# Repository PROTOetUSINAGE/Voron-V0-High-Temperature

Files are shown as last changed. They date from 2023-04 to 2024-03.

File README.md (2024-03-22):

# Voron_V0_High_Temperature

The idea  was to make a Voron V0 with the capability of printing high temperature materials like PEI, PEEK ...

A lot of rework was made to be able to fit everything.

I don't even know if we can still call it a Voron V0.

By accident, I maybe design the Smallest High Temp 3D Printer.

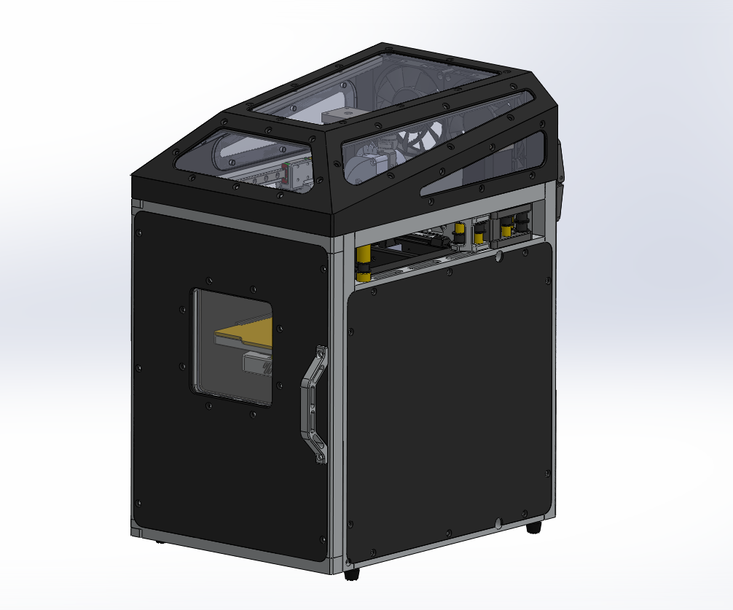
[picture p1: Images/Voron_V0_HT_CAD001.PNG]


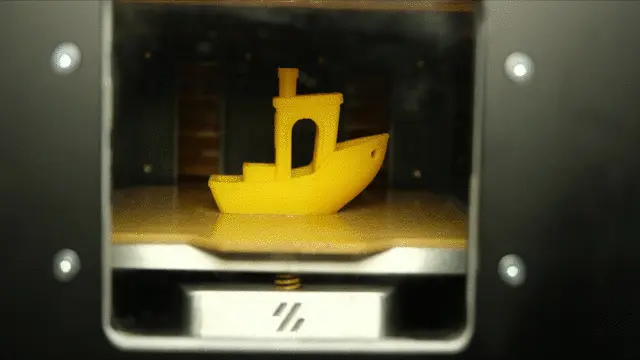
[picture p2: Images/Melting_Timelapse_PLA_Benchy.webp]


## Caracteristics :

- Print volume : 115x115x115mm( a little bits smaller than a V0 )
- Max speed : 500mm/s at 20000mm/s² acceleration
- Max printing speed : around 250mm/s
- Duet3D mini 5+ control board
- Bondtech Mini LGX extruder
- 24V PSU
- Watercooled Hotend Dragon Highflow up to 450°C
- 60W cartridge Heater for the hotend
- Compatible with V6 nozzle ( so I can use brass, copper, steel, ... nozzle )
- Force convection heated chamber up to 230°C 
- 400W 230V cartridge heater with fins for the chamber
- Ø100mm aluminium blower power by a bldc motor 
- Glass fiber reinforce PEI bed
- 100W 230V Silicone heater pad for the bed
- 250°C thermal fuse to protect my house from fire
- Tig welded steel chamber 1mm thick sheet
- CNC milled frame and gantry
- Tig welded aluminium hood with polycarbonate windows and leds
- Custom clamp mechanism for the bed 
- Custom bellow made from PI ( Kapton and PTFE tape)
- Door with borosilicate double glazing 
- Milled Dibond panel
- 7 fans if you count the blower
- The few parts who are 3d printed are made of PEKK-CF
- The printer weighs 10kg ( which is a lot for it size )
- Almost same fooprint as the V0 230x300mm

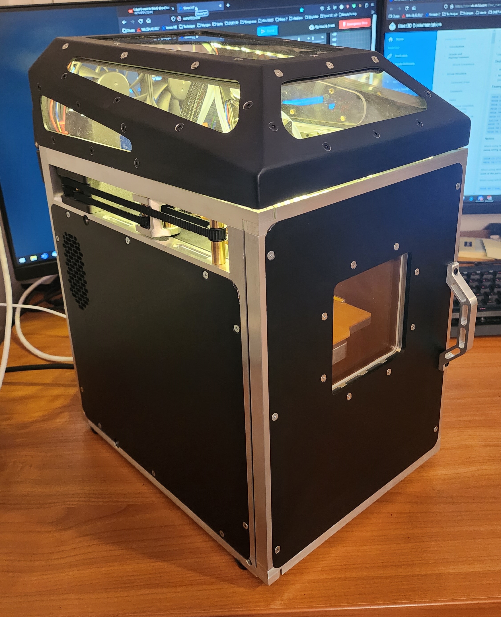
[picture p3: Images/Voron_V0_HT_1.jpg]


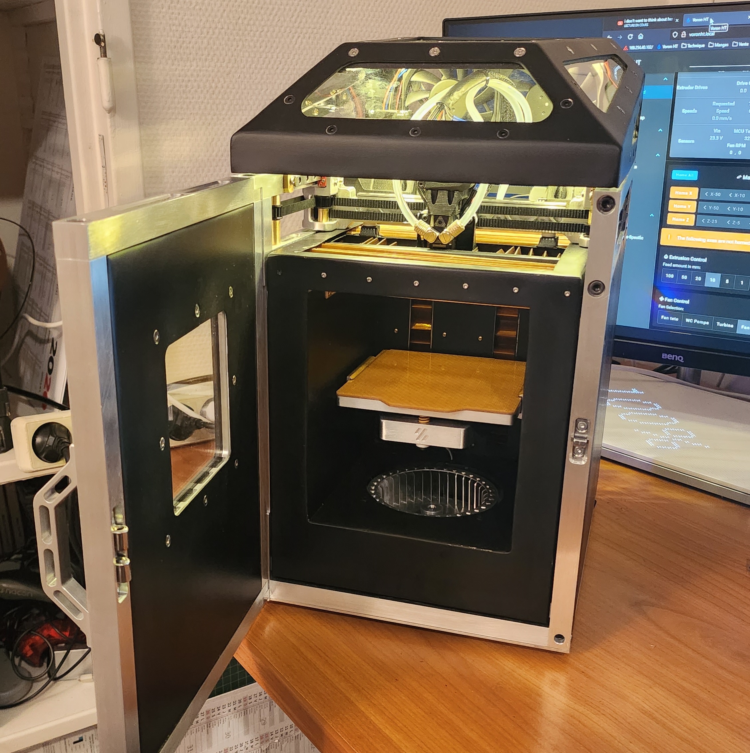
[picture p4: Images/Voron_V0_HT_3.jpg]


Around 800hr was needed to make the first example.

If you want to discuss of the build : [Discord](https://discord.com/channels/840596987522056232/1103065458917261322)

Disclaimer : This build is not supported by Voron Design

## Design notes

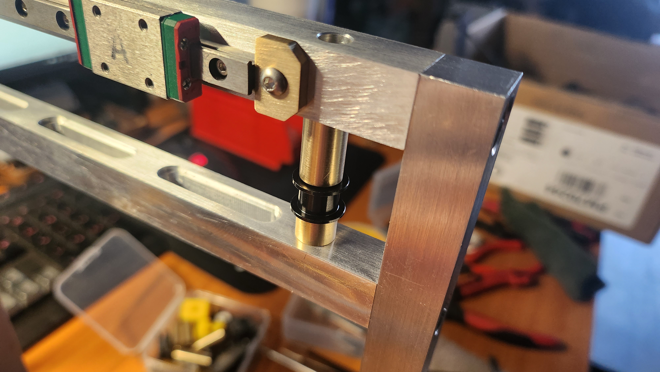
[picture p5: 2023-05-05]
Images/Voron_V0_HT (88).jpg

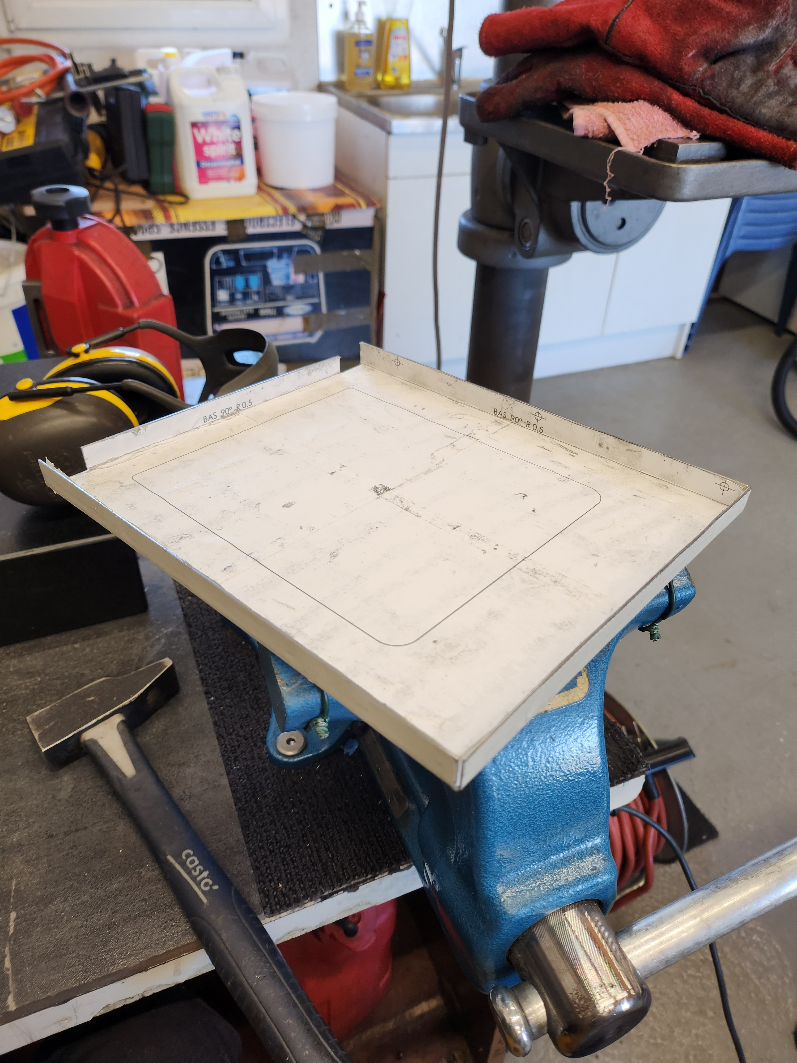
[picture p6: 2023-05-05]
Images/Voron_V0_HT (17).jpg

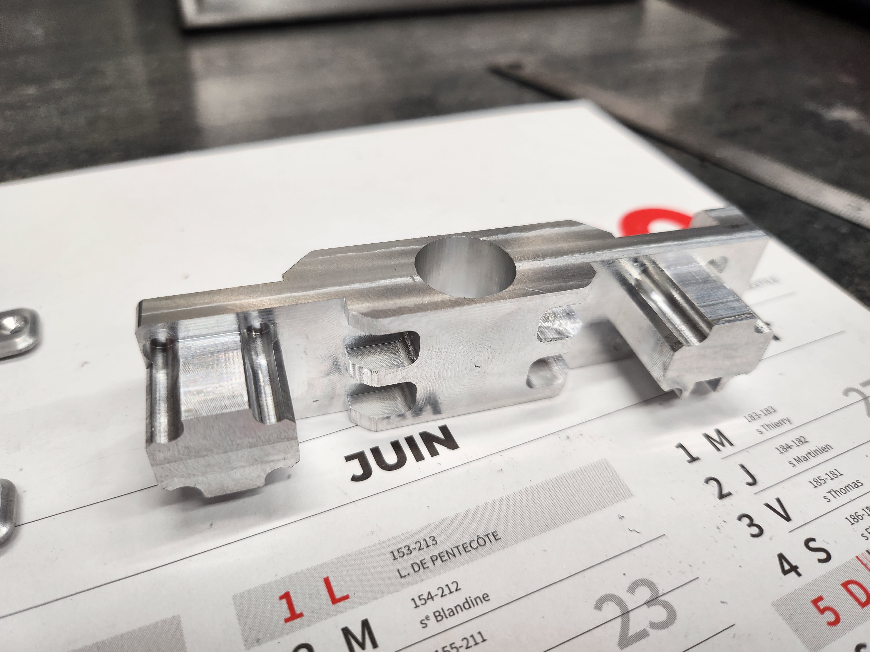
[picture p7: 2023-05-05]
Images/Voron_V0_HT (58).jpg

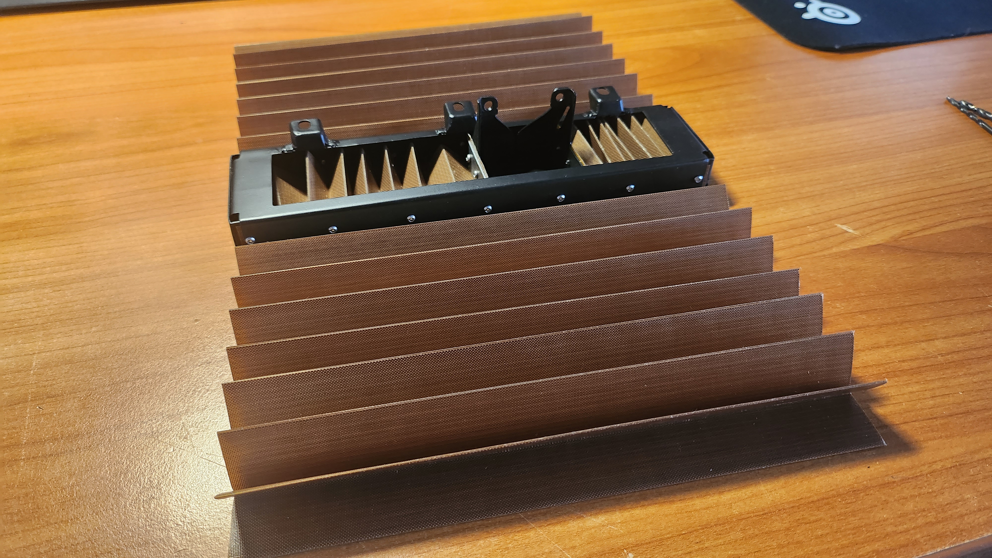
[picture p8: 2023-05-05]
Images/Voron_V0_HT (102).jpg

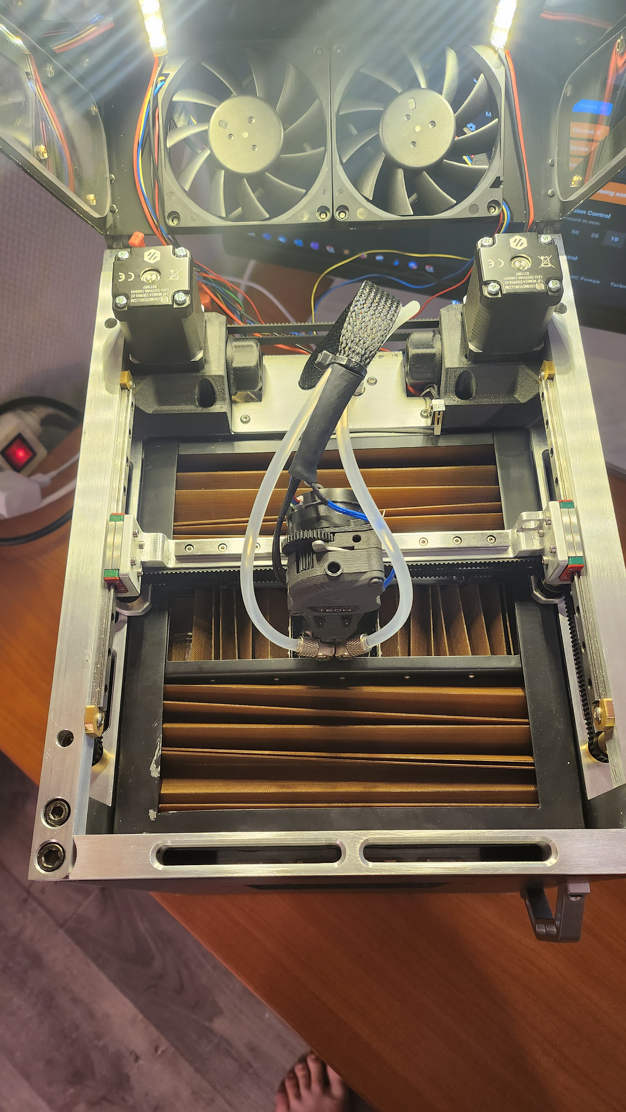
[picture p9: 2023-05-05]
Images/Voron_V0_HT (114).jpg

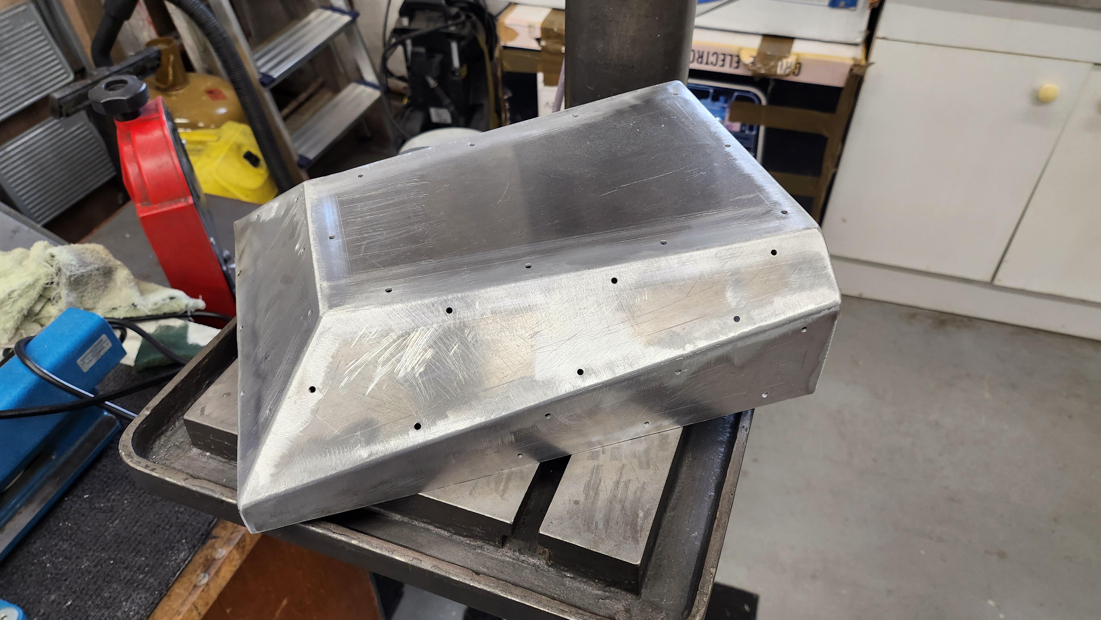
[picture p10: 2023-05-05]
Images/Voron_V0_HT (66).jpg

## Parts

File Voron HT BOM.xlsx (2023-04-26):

Components |  | QTY | Link | Price | Comment
 |  |  | Total = | 1338.70 €
Hardware | M3 Rivnut
 | M3 Brass Insert
 | M3 ceramic washer
 | M5
 | M3
 | M2
Printed parts | Spool_Holder | 1
 | Hood_Hinge_Male | 2
 | Hood_Hinge_Female | 2
 | Hood_LED_Support | 1
 | DC-DC_Converter_Support | 1
 | Cover_230V | 1
 | PSU_Support | 1
 | X_Carriage | 1
 | Cable_Chain_Support | 1
 | Tensioner_Knob | 2
 | BLDC_Support | 1
 | Drive_Tensioner | 2
 | Drive_Frame | 1
 | Drive_Frame_Symmetry | 1
 | Stress_Relief_Bracket | 1
 | Railstop | 8
Machined parts | Window_Support | 1
 | Door_Handle | 1
 | Door_Pivot | 2
 | Front_Cover | 1
 | Hot_Air_Exit | 2
 | Door_Frame | 1
 | Chamber_Fan_Shaft | 1
 | Chamber_Fan_Bearing_Housing | 1
 | Impeller_Cover | 1
 | Bed_Support | 1
 | Z_Support | 1
 | Bed_Clamp | 2
 | Bed | 1
 | Spacer_M3_Ø8 | 6
 | Gantry | 1
 | Spacer_M3_Ø12_Short | 2
 | Spacer_M3_Ø12_Long | 2
 | Side_Cover_Ventilated | 1
 | Side_Cover | 1
 | Frame | 1
Sheet metal parts | Front_Door | 1
 | Radiator_Support | 1
 | Bellow_Clamp_Z | 4
 | Bellow_Clamp_Z_2 | 4
 | Bellow_Clamp_X | 2
 | Bellow_Clamp_Z | 2
 | Fixing_Lug | 3
 | Bottom_Heated_Chamber | 1
 | Inside_Wall | 2
 | L_Heated_Chamber | 2
 | Bellow_Frame | 2
 | Rear_Chamber | 1
 | Middle_Airflow_Path | 1
 | Back_Airflow | 1
 | Front_Airflow | 1
 | Back_Chamber | 1
 | Gantry_Frame_Clamp | 1
 | Heater_Block_Frame | 1
 | Heater_Block_Plate | 1
 | Gantry_Frame | 1
 | Front_Chamber | 1
 | Endstop_Finger | 1
 | Bed_Spring_Clamp | 1
 | Electronic_Access_Plate | 1 |  | 10.00 €
 | Bottom_Plate | 1 |  | 10.00 €
 | Electronic_Plate | 1 |  | 10.00 €
Metal | 15x15X500mm 2017A | 15 |  | 126.00 €
 | 15x162x162 2017A | 1 |  | 29.89 €
 | 50x50x500mm 2017A | 1 |  | 60.30 €
 | 5x120x248mm 2017A | 1 |  | 10.89 €
 | 20x20X500mm 2017A | 1 |  | 11.13 €
 | Ø10x500mm laiton | 1 |  | 6.20 €
 | 3x20x500mm laiton | 1 |  | 5.54 €
 | 1mm Steel Sheet Carbon Steel | 1 |  | 20.00 €
Chamber | 230V Heater Cartridge with fins 200w 80mm | 2 | Aliexpress (https://fr.aliexpress.com/item/1005003240961756.html) | 43.80 €
 | Ø100mm Blower | 1 | Aliexpress (https://fr.aliexpress.com/item/2003966058.html) | 15.45 €
 | Bldc motor 4260 | 1 | Aliexpress (https://fr.aliexpress.com/item/1005003795771959.html) | 24.99 €
 | 60th Pulley GT2 Ø6 | 1 | Aliexpress (https://fr.aliexpress.com/item/1005003339656144.html) | 3.71 €
 | Circlips Ø22mm
 | Bearing 608 2ZZ
 | Silicone grease
 | Courroie gt2 6mm 400lg | 1 | 123courroie (https://www.123courroies.com/courroie-dentee-2mgt-pas-2mm-renforcee/300696-courroie-dentee-400-2mgt6-gates-5414465285899.html) | 8.48 €
Electronics | PSU 150W 24V DC | 1 | Amazon (https://www.amazon.fr/NUOVA-GERMANY-Alimentation-Professionnelle-Transformateur/dp/B09MJHLBQ7) | 17.90 €
 | Raspberry Pi | 1 | Kubii (https://www.kubii.com/fr/cartes-raspberry-pi/2119-raspberry-pi-3-modele-b-1-gb-kubii-652508442174.html) | 52.80 €
 | Duet3 mini 5+ Wifi | 1 | Caribou (https://caribou3d.com/en/electronic-boards-displays/854-duet3-mini5-wifi.html) | 145.00 €
 | NEMA14 Stepper Motor 40Ncm | 2 | Aliexpress (https://fr.aliexpress.com/item/1005002583135981.html) | 86.39 €
 | NEMA17 Stepper Motor (34mm max) with integrated lead screw 200mm T8x8 | 1
 | NEMA14 36mm round pancake Stepper Motor with 10 tooth spur gear (LDO 36STH20-1004AHG) | 1
 | Omron Mouse Button - Micro Switch | 3 | Amazon (https://www.amazon.fr/gp/product/B081TXMD4K/ref=ppx_yo_dt_b_asin_title_o04_s00?ie=UTF8&th=1) | 8.00 €
 | AC Inlet | 1 | Amazon (https://www.amazon.fr/Willwin-IEC320-C14-Inlet-connecteur-Interrupteur-Commutateur/dp/B078PFFL46) | 1.71 €
 | C13 Power Cord | 1
 | Thermal fuse ceramic 230°C 230V 10A | 1 | Aliexpress (https://fr.aliexpress.com/item/32885492280.html) | 0.73 €
 | Fan Noctua NF-A4x20 FLX 12v | 2 | Amazon (https://www.amazon.fr/gp/product/B071J8CZP9/ref=ppx_yo_dt_b_asin_title_o01_s01?ie=UTF8&psc=1) | 29.80 €
 | Stepdown converter DC-DC 5A 5-32V | 2 | Amazon (https://www.amazon.fr/gp/product/B07VQ89RZG/ref=ppx_yo_dt_b_asin_title_o00_s00?ie=UTF8&psc=1) | 8.99 €
 | PT1000 | 3 | Aliexpress (https://fr.aliexpress.com/item/1005003923279506.html) | 54.12 €
 | Hood fan Delta EFC0812DB | 2 | Mouser (https://www.mouser.fr/ProductDetail/Delta-Electronics/EFC0812DB-F00?qs=%2FW4LtXOBxKstDt5MAdb1kQ%3D%3D) | 27.06 €
 | Fan _70mm | 2 | Amazon (https://www.amazon.com/Gelid-Solutions-Silent-40mm-FN-SX04-42/dp/B00BF3UJKC?ref_=ast_sto_dp&th=1) | 16.00 €
 | SSR_10A_240VAC-32DC | 2 | Mouser (https://www.mouser.fr/ProductDetail/Omron-Automation-and-Safety/G3NA-220B-UTU-DC5-24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) | 76.00 €
 | 24V Heater Cartridge 60w | 1 | Aliexpress (https://fr.aliexpress.com/item/4000974620358.html) | 13.52 €
Extruder Hardware | Watercooled Dragon Hotend | 1 | Aliexpress (https://fr.aliexpress.com/item/1005003231830302.html) | 86.86 €
 | Bondtech lgx lite | 1 | 3Djake (https://www.3djake.fr/bondtech/extrudeuse-lgx-lite-sans-moteur-pas-a-pas) | 69.98 €
 | V6 nozzle 0,4mm | 1 |  |  | 1 nickel plated brass nozzle with dragon hotend
Buildplate | Silicone AC 230V Heater 100x100mm 100W | 1 | Aliexpress (https://fr.aliexpress.com/item/1005002731504740.html) | 28.27 €
 | Aluminum Build Plate 120x120mm 8mm Thickness | 1 |  | 10.00 €
 | Yellow die springs 8x4x20mm | 3 | Aliexpress (https://fr.aliexpress.com/item/32977566403.html) | 5.33 €
Motion | MGN7H Linear Rail 150mm | 5 | Aliexpress (https://fr.aliexpress.com/item/1005001843434827.html) | 55.70 €
 | T8 flange Nut 8mm Lead | 1 | Aliexpress (https://fr.aliexpress.com/item/1005002583135981.html) |  | With kit motor
 | GT2 Open Belt 6mm (3 meters) | 1 | Aliexpress (https://fr.aliexpress.com/item/32987817703.html) | 22.35 €
 | GT2 20T (6mm wide) (5mm bore) | 3 | Aliexpress (https://fr.aliexpress.com/item/32995102911.html) | 9.73 €
 | GT2 idler with teeth | 2 | Aliexpress (https://fr.aliexpress.com/item/1005002998469233.html) | 2.18 €
 | GT2 idler without teeth | 10 | Aliexpress | 10.90 €
Watercooling | Radiator 40mmx2 Alphacool | 1 | Aquatuning (https://www.aquatuning.fr/refroidissement-par-eau/radiateurs/radiateurs-aktiv/40mm/15906/alphacool-nexxxos-xt45-plein-de-cuivre-40mm-dual-radiateur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) | 38.79 €
 | Pump G1/4 | 1 | Aliexpress (https://fr.aliexpress.com/item/1005003646698710.html?scm_id=1007.40050.281175.0&scm-url=1007.40050.281175.0) | 21.16 €
Misc. | 7mm x 7mm cable chain | 1 | Aliexpress (https://www.aliexpress.com/p/order/detail.html?orderId=3016825993495175) | 3.20 €
 | Rubber Feet (14x11x9mm) | 4 | Aliexpress (https://fr.aliexpress.com/item/33014925172.html) | 0.28 €
 | Bowden Tubing 4mmOD 2mmID (1 meter) | 1
 | Adesive tape PTFE | 2 | Amazon (https://www.amazon.fr/Haute-Temp%C3%A9rature-Ruban-Cizen-Adh%C3%A9sif/dp/B07FNRR5DZ) | 11.96 €
 | 2mm Polycarbonate Sheet | 1
 | Lock | 1 | Aliexpress (https://fr.aliexpress.com/item/32899592678.html) | 5.21 €
 | Dibond sheet 3mm | 1
 | 2mm PEI Glassfiber Sheet | 1
 | 1mm PTFE Sheet | 1 | Amazon (https://www.amazon.fr/gp/product/B00DYZGYQM/ref=ppx_yo_dt_b_asin_title_o09_s00?ie=UTF8&psc=1) | 8.40 €
 | Borosilacate glass 100mmx100mm x3mm | 2 | Amazon (https://www.amazon.fr/gp/product/B07YXFKMXV/ref=ppx_od_dt_b_asin_title_s00?ie=UTF8&psc=1) | 14.00 €

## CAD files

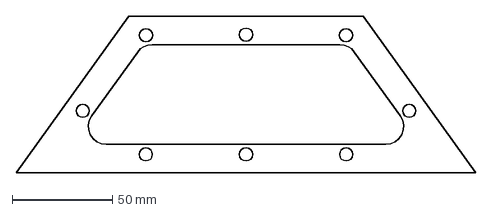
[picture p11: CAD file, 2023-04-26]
DXF/Hood_Frame_Front_Slope.DXF
229.0 x 77.8 mm

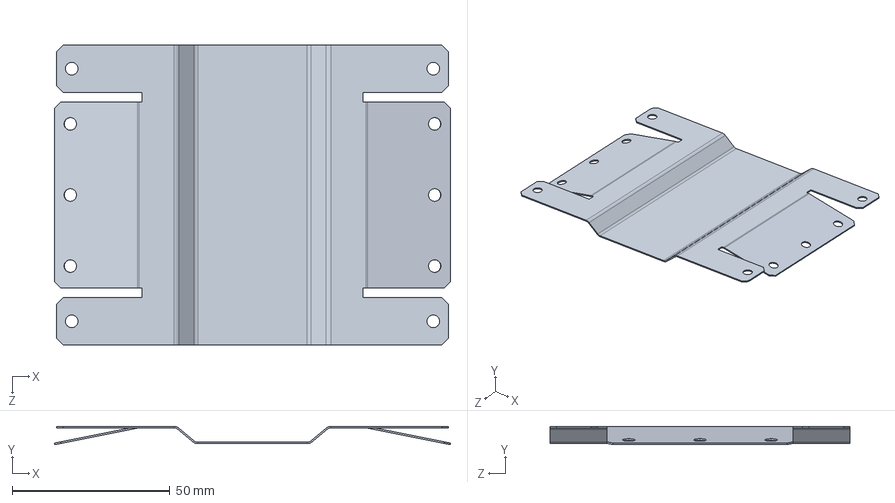
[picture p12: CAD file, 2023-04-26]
STEP/Bed_Clamp_Spring.STEP
125.4 x 5.79 x 95.0 mm

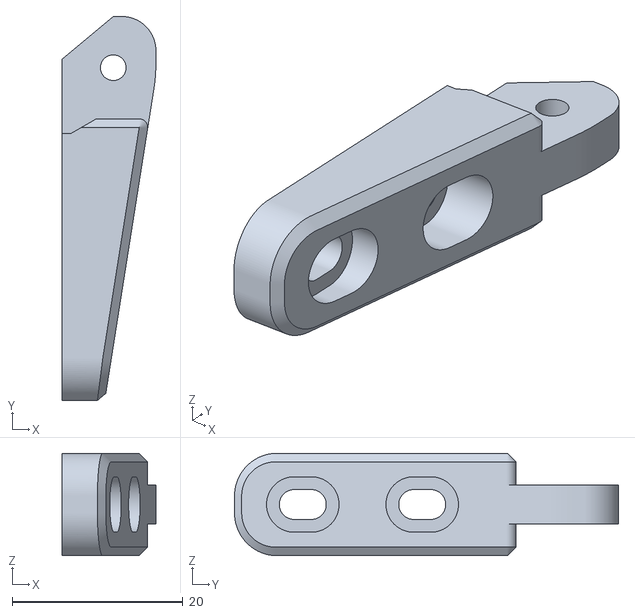
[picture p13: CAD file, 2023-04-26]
STL/Hood_Hinge_Male.STL
11.0 x 45.0 x 12.0

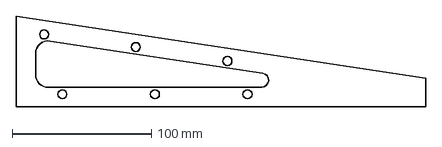
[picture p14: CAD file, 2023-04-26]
DXF/Hood_Frame_Side.DXF
294.0 x 65.0 mm

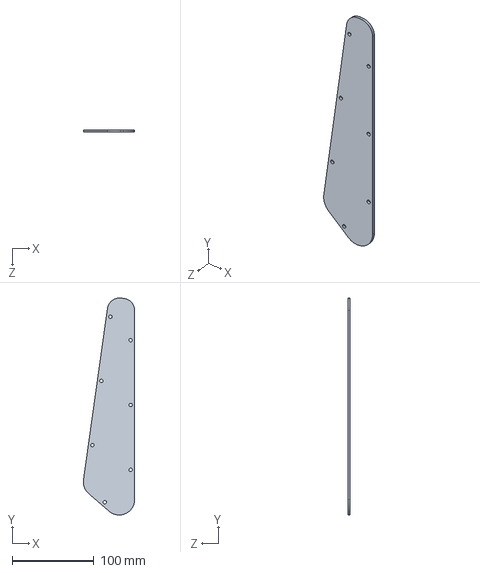
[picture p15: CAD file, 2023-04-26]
STEP/Window_4.STEP
63.0 x 266.2 x 3.00 mm

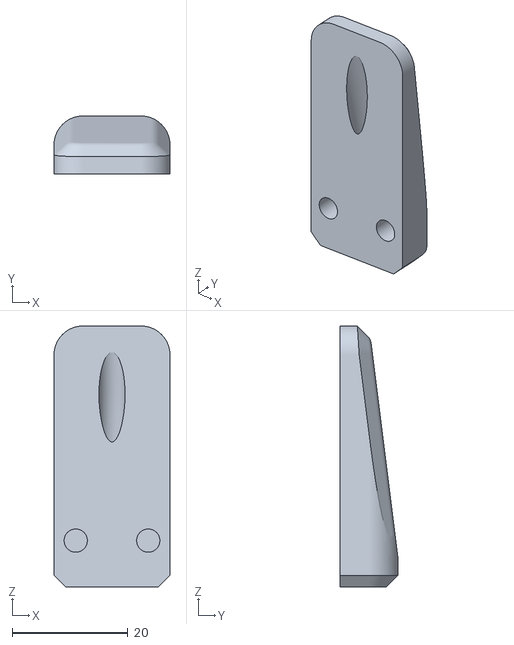
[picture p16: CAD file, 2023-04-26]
STL/Pathtrough.STL
20.0 x 10.00 x 45.0

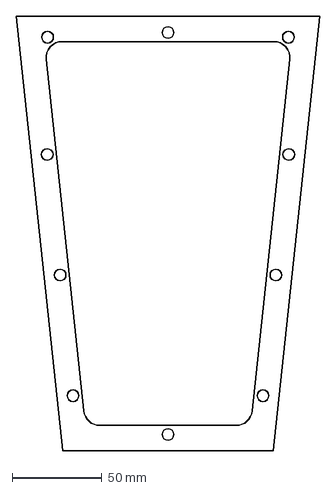
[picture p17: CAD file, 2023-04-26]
DXF/Hood_Frame_Top.DXF
169.0 x 241.5 mm

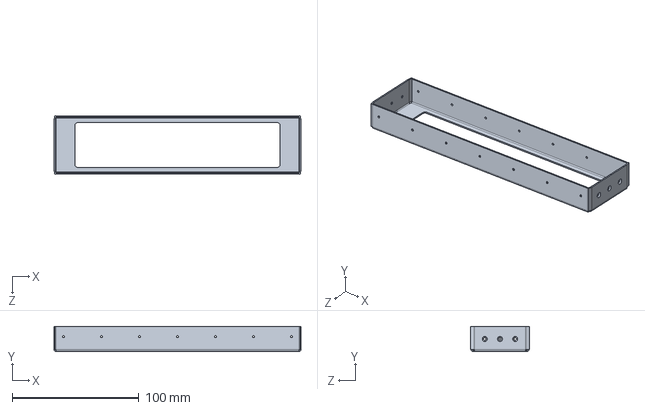
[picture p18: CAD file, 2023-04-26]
STEP/Gantry_Frame.STEP
195.0 x 20.0 x 46.4 mm

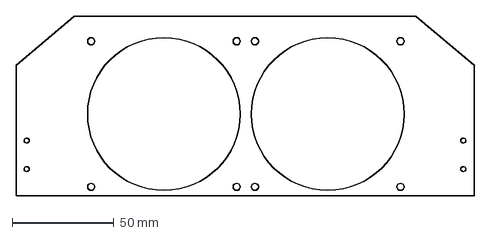
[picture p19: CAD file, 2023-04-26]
DXF/Hood_Frame_Rear.DXF
225.0 x 88.0 mm

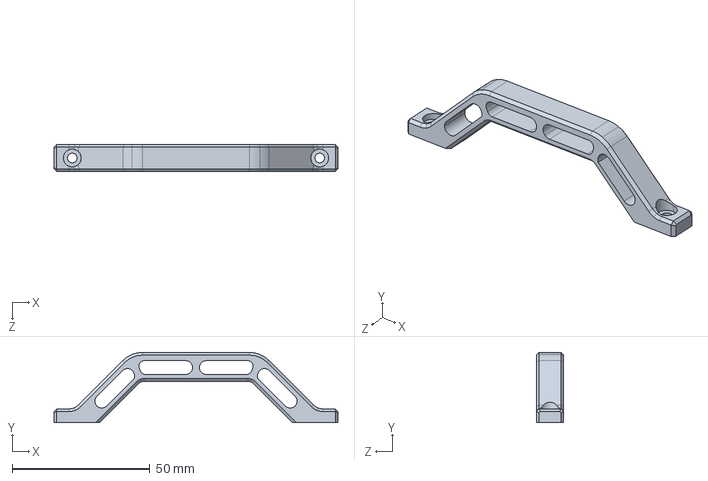
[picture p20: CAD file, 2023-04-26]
STEP/Door_Handle.STEP
103.3 x 25.5 x 10.0 mm

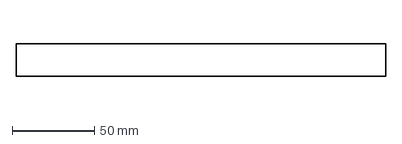
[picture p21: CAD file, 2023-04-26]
DXF/Hood_Frame_Front.DXF
225.0 x 20.0 mm

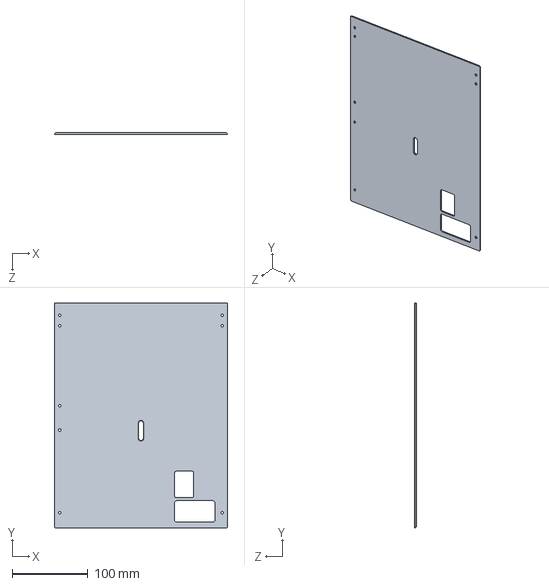
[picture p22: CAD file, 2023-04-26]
STEP/Electronic_Access_Plate.STEP
229.0 x 297.0 x 2.00 mm

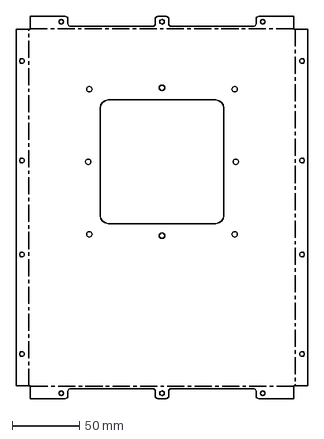
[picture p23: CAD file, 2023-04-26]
DXF/Front_Door.DXF
216.5 x 284.5 mm

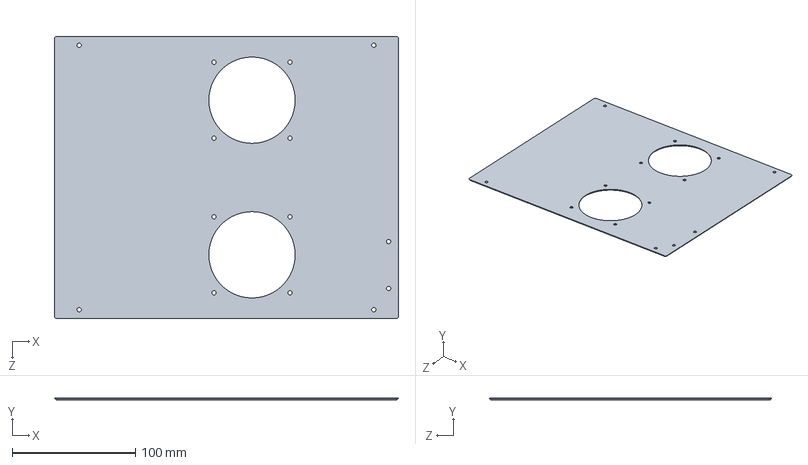
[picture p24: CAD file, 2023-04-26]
STEP/Bottom_Plate.STEP
279.0 x 2.00 x 229.0 mm

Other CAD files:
DXF/Hood_Frame_Side_Slope_Left.DXF
STEP/Bed_Clamp.STEP
STEP/Tensioner_Knob.STEP
STEP/Bottom_Heated_Chamber.STEP
DXF/Back_Airflow.DXF
DXF/Back_Chamber.DXF
DXF/Bed_Clamp_Spring.DXF
DXF/Bellow_Clamp_X.DXF
DXF/Bellow_Clamp_Y_Axis.DXF
DXF/Bellow_Clamp_Z.DXF
DXF/Bellow_Clamp_Z_2.DXF
DXF/Bellow_Frame.DXF
DXF/Bottom_Heated_Chamber.DXF
DXF/Bottom_Plate.DXF
DXF/Door_Seal_Viton.DXF
DXF/Electronic_Access_Plate.DXF
DXF/Electronic_Plate.DXF
DXF/Endstop_Finger.DXF
DXF/Fixing_Lug.DXF
DXF/Front_Airflow.DXF
DXF/Front_Chamber.DXF
DXF/Front_Cover.DXF
DXF/Gantry_Frame.DXF
DXF/Gantry_Frame_Clamp.DXF
DXF/Heater_Block_Frame.DXF
DXF/Heater_Block_Plate.DXF
DXF/Inside_Wall.DXF
DXF/L_Heated_Chamber.DXF
DXF/Middle_Airflow_Path.DXF
DXF/PEI_Bed.DXF
DXF/PTFE_Door_Spacer.DXF
DXF/Pump_Support.DXF
DXF/Radiator_Support.DXF
DXF/Rear_Chamber.DXF
DXF/Side_Cover.DXF
DXF/Side_Cover_Ventilated.DXF
DXF/Window_1.DXF
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
